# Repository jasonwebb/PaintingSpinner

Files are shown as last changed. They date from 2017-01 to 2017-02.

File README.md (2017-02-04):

# PaintingSpinner
Arduino-based hardware platform for interactively spinning a painting using a DC motor, infrared rangefinder and custom 3D printed components.

## Components

- Arduino Uno R3
- A [99:1, 300oz-in gearmotor](https://www.pololu.com/product/3207) driven by a [Cytron 10A DC Motor Driver Shield](http://www.robotshop.com/en/10a-dc-motor-driver-arduino-shield.html)
- Two 3W speakers driven by a [Cytron Easy MP3 Shield](http://www.robotshop.com/en/cytron-easy-mp3-shield.html)
- A [Sharp 2Y0A02 distance sensor](https://www.sparkfun.com/products/8958)
- Salvaged bicycle parts (chain, 26t and 14t gears)
- Various sizes of [scrap wood](https://github.com/jasonwebb/PaintingSpinner/blob/master/BOMs/Wood%20cutlist.csv)
- Various custom [3D printed parts](https://github.com/jasonwebb/PaintingSpinner/tree/master/CAD) designed in Fusion 360
- Various wood screws and angle brackets

## License
This work is licensed under a [Creative Commons Attribution-NonCommercial-ShareAlike 4.0 International License](http://creativecommons.org/licenses/by-nc-sa/4.0/).

Use this project to learn, tinker and share with friends. All commercial uses are forbidden without express written permission.



## Electronics architecture
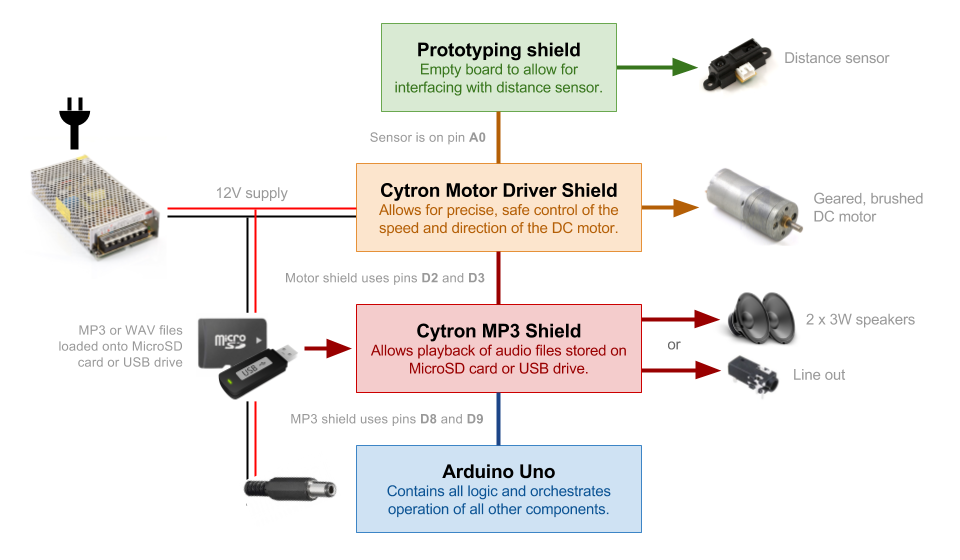
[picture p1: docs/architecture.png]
Architecture


## Mechanical assembly
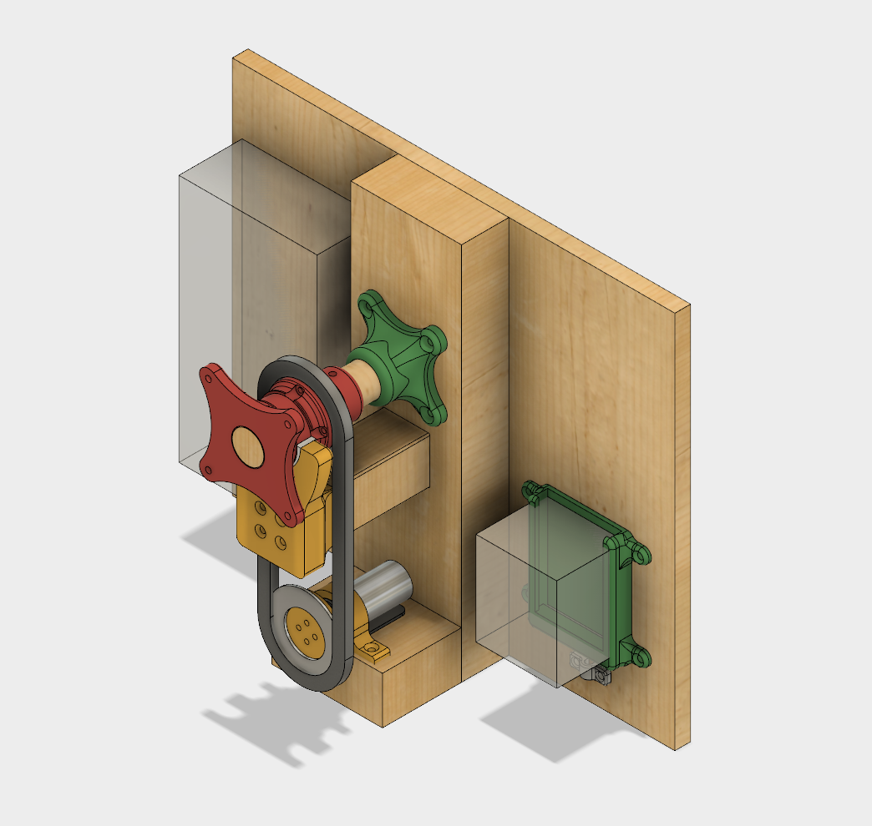
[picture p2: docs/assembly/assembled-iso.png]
Assembly


## Finished and installed
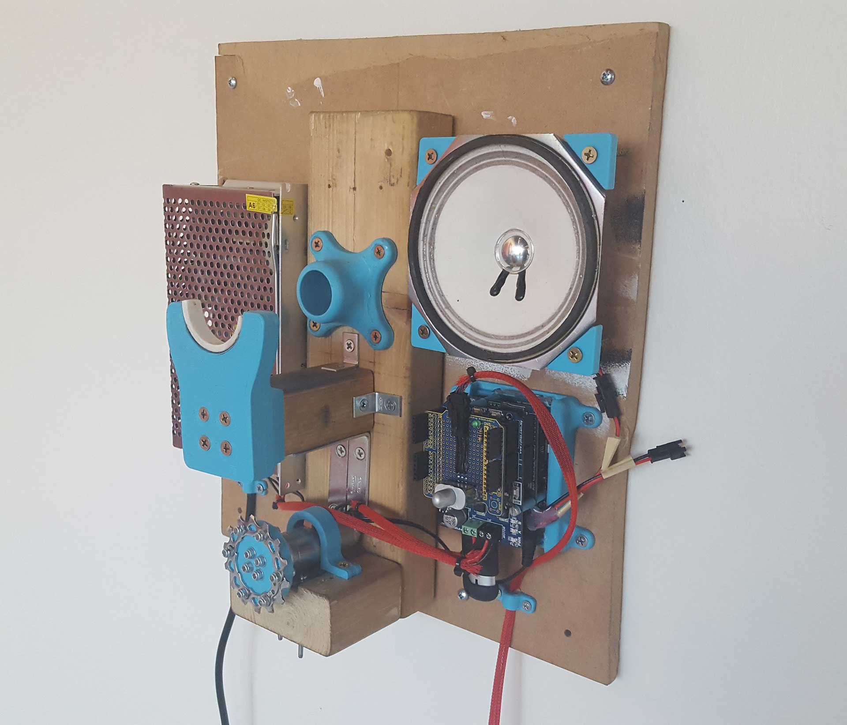
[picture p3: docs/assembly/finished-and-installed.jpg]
Finished and assembled


Nadia approaching

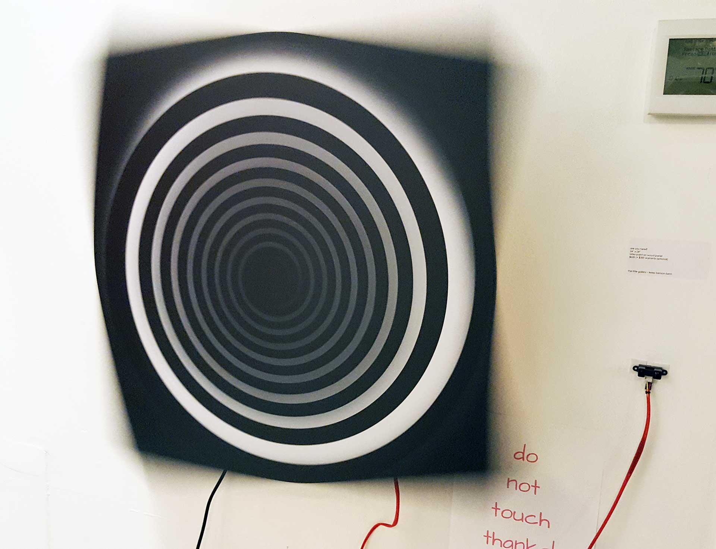
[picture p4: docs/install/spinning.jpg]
Spinning


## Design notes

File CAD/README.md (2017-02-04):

## Arduino stack standoffs
- Intended to guarantee uniform and reliable spacing between shields, reducing potential of shorts or disconnections due to tilting during use.
- Long standoffs (green) go between motor shield and audio shield.
- Short standoffs (yellow) go between audio shield and Arduino.
- Red washers go at very top of bolt.

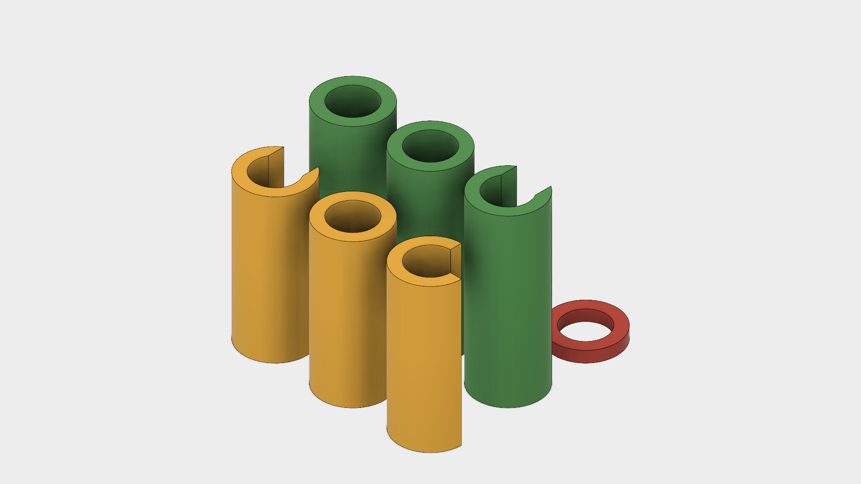
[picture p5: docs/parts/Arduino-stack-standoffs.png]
Arduino stack standoffs


## Axle support bracket
- Square cutout designed to loose friction fit with 2" square furring strip, which has nominal size of ~1.5".
- Circular cutout is made to fit half of a 1.5" diameter PVC tubing, cut to 1/2" in width. Use epoxy to join. This PVC inset will make direct contact with recessed ridge in "Compound pulley flange" allowing for smooth rotation and (hopefully) less friction.

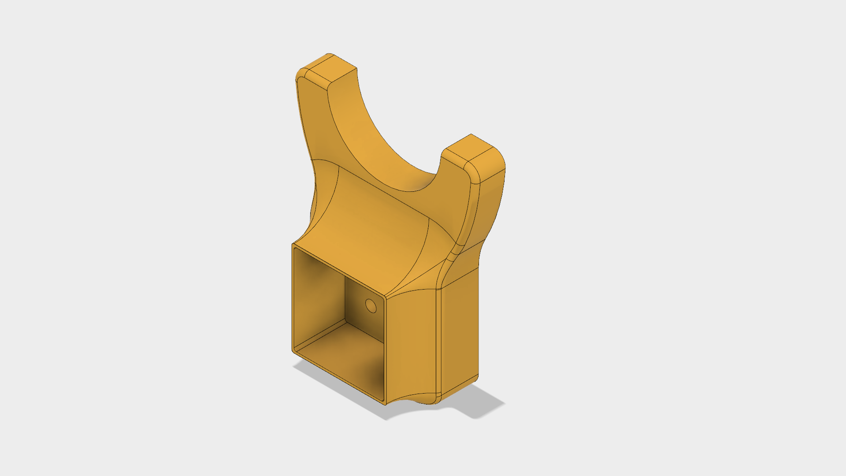
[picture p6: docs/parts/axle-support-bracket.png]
Axle support bracket


## Compound pulley flange
- One side (side with four arms) mounts to back of painting or piece to spin.
- Other side fits a 14t bicycle gear with particular hole pattern using M3 bolts.
   - Hole pattern is rotated to make it easier for a screwdriver to reach bolt heads for tightening / racheting.
- Includes a 1/2" wide recessed ridge meant to guide rotation of entire component along PVC inset on "Axle support bracket"
- A 1" wooden dowel goes through center hole, optionally fastened with small wood screw within recessed ridge. Make sure the head of the screw stays below diameter of this ridge to avoid interfering with rotation.

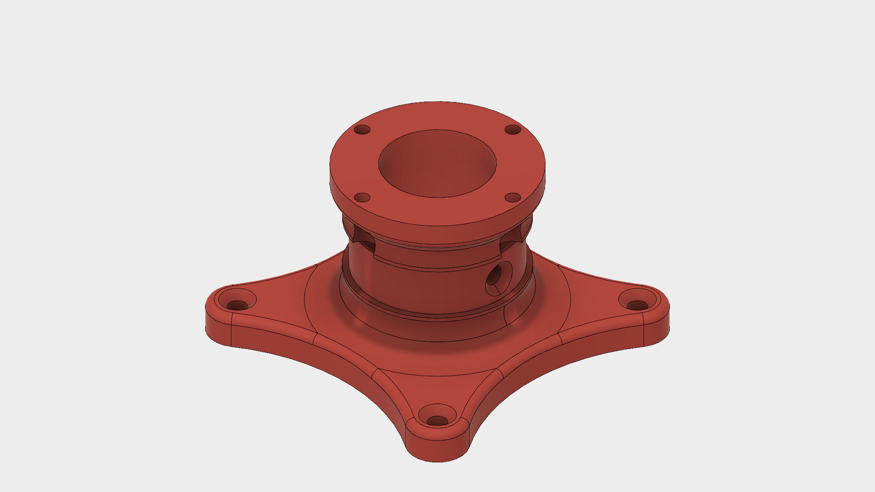
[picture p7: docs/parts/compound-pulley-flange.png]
Compound pulley flange


## Flange (right angle)
- Center hole has clearance fit allowance in order for 1" wood dowel to spin freely.
- Only meant to constrain wood dowel during rotation.

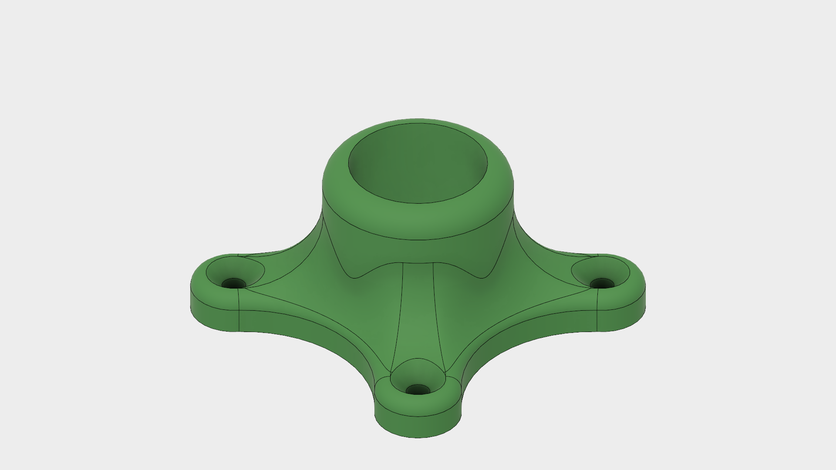
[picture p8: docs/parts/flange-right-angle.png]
Flange right angle


## Large pulley (26t) to Universal Mounting Hub adapter
- Allows for mounting of a 26t with a particular hole pattern to a Universal Mounting Hub from Pololu.
- Uses M4 bolts (with washers and lock nuts) to connect adapter to pulley.
- Uses M3 bolts (with lock nuts under adapter) to connect adapter to Universal Mounting Hub.

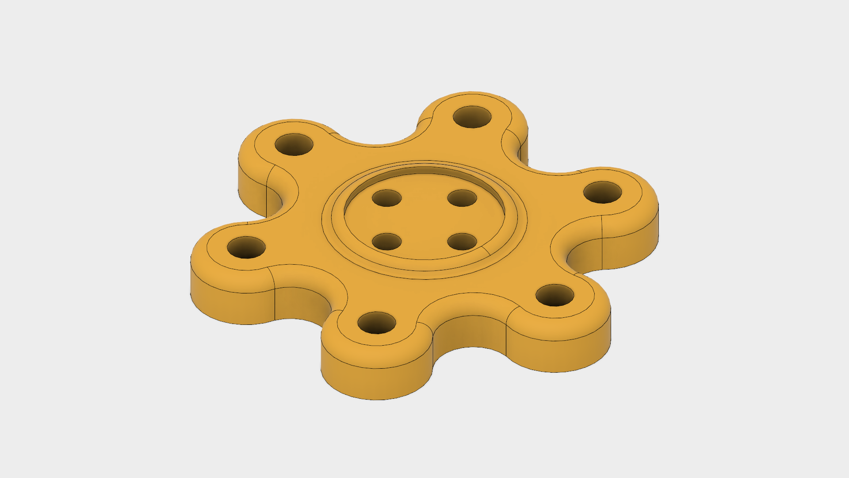
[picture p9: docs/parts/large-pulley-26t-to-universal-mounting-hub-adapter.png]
Large pulley (26t) to Universal Mounting Hub adapter


## Motor clamp
- Snuggly fits around gearmotor to help hold it in place. Use two wood screws to get desired level of tension.
- I recommend only using one directly over the gearbox, NOT the motor, to allow for better heat dissipation.

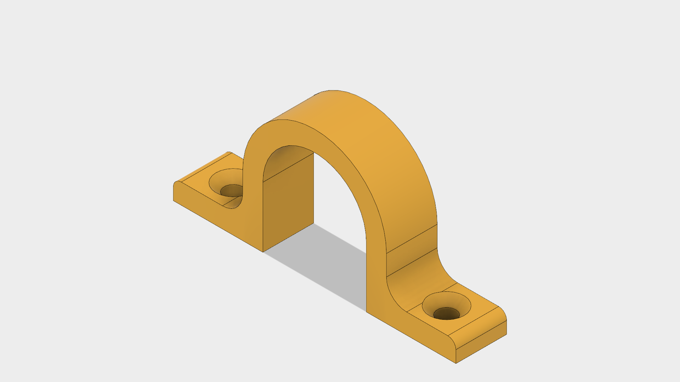
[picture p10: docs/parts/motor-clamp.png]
Motor clamp


## Small pulley (14t) flange
- Center hole fits 1" wood dowel.
- Meant to be bolted onto 14t bicycle gear with a particular hole pattern.
- Meant to accommodate M3 lock nuts with enough clearance to allow for a ratchet for easier tightening.

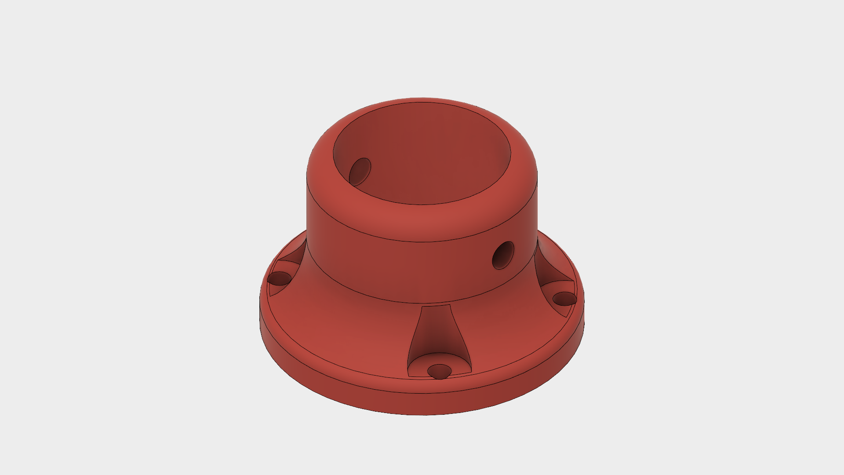
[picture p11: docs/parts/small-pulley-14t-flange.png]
Small pulley (14t) flange


## Small pulley (14t) to Universal Mounting Hub adapter
- Uses M3 bolts for all holes.
- Allows for use of drive pulley matching output pulley for better torque (at lower speed).

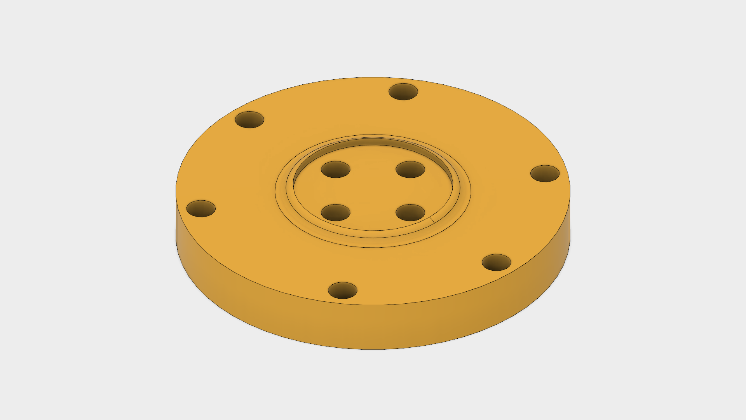
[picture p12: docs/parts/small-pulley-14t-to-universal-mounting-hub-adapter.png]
Small pulley (14t) to Universal Mounting Hub Adapter


## Speaker corner bracket
- Made to fit metal corner tabs for a particular speaker.

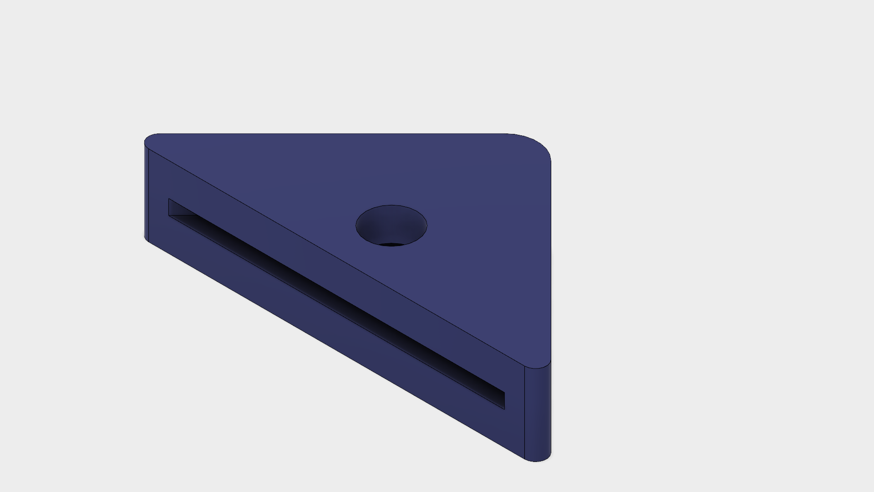
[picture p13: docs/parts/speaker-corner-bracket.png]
Speaker corner bracket


## Wire clamp
- Allows for strain relief for thicker wires, such as the AC power cord and sensor cable. Saves a trip to the hardware store at least.

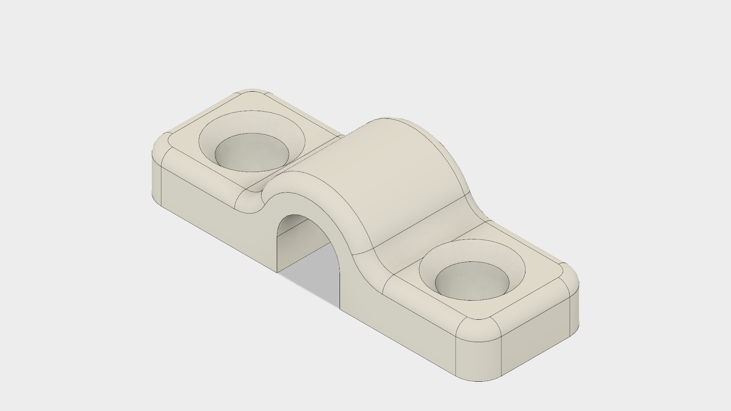
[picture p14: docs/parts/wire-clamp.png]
Wire clamp


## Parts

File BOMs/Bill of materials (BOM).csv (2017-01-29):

Part | Model name | Cost | Dealer | URL | Use
Motor | 99:1 Metal Gearmotor 25Dx54L mm HP 12V | $21.95 | Pololu | https://www.pololu.com/product/3207 | Uhm...it spins.
Mounting hub | Pololu Universal Aluminum Mounting Hub for 4mm Shaft, M3 Holes (2-Pack) | $6.95 | Pololu | https://www.pololu.com/product/1997 | Connecting motor shaft to painting
Motor mounting bracket | Pololu 25D mm Metal Gearmotor Bracket Pair | $7.45 | Pololu | https://www.pololu.com/product/2676 | Allows for easy, strong mounting of motor to box
Motor driver | 10A DC Motor Driver Arduino Shield | $15.75 | Robotshop | http://www.robotshop.com/en/10a-dc-motor-driver-arduino-shield.html | Allows Arduino to control the motor speed and direction
Arduino | Arduino Uno R3 (official) | $22.39 | Robotshop | http://www.robotshop.com/en/arduino-uno-r3-usb-microcontroller.html | Contains all logic and coordinates all other components
MP3 shield | Cytron Easy MP3 Shield | $17.06 | Robotshop | http://www.robotshop.com/en/cytron-easy-mp3-shield.html | Allows Arduino to play and control audio - can play through 3 small speakers or audio cable
SD card or USB drive | {On hand?} |  |  |  | Stores MP3 files for playback
Speakers | {Need two 3W speakers - on hand?}
Power supply | LEDMO 12V @ 20A power supply | $17.99 | Amazon | https://smile.amazon.com/LEDMO-Switching-Converter-Adapter-Transformer/dp/B01E6S0JS4 | Supplies power to everything
Prototyping shield | ProtoShield Short Prototyping Board for Arduino | $2.25 | Robotshop | http://www.robotshop.com/en/protoshield-short-prototyping-board-arduino.html | Allows for freeform interfacing with sensor(s)
Distance sensor | Sharp GP2Y0A02YK0F | $14.95 | Sparkfun | https://www.sparkfun.com/products/8958 | Sensing the viewer for interactivity
 | Total | $126.74

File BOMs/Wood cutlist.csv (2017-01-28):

Name | Material | Dimension(s) - inch | Dimension(s) - mm
Axle | 1" wood dowel | 5 in
Axle support | 2" square furring strip | 3.89 in | 98.806mm
Motor support | 2x4" stud | 2.5 in
Mounting spine | 2x4" stud | 12 in
Mounting plate | Plywood - 0.5" or more | At least 14x12"

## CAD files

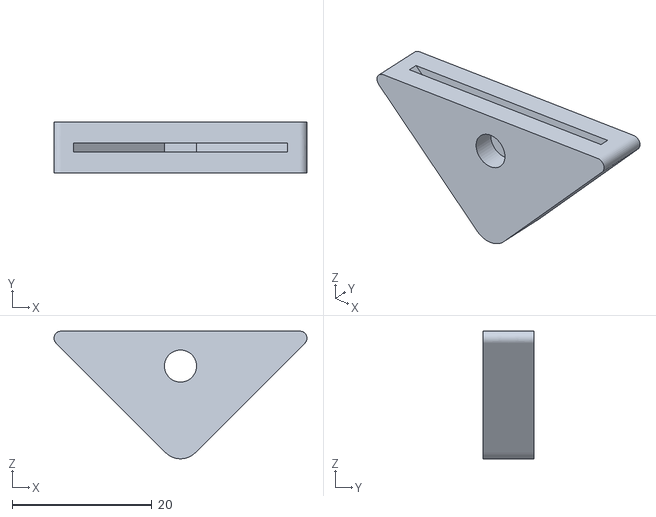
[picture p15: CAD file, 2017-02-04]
CAD/speaker-corner-bracket.stl
36.3 x 7.35 x 18.3

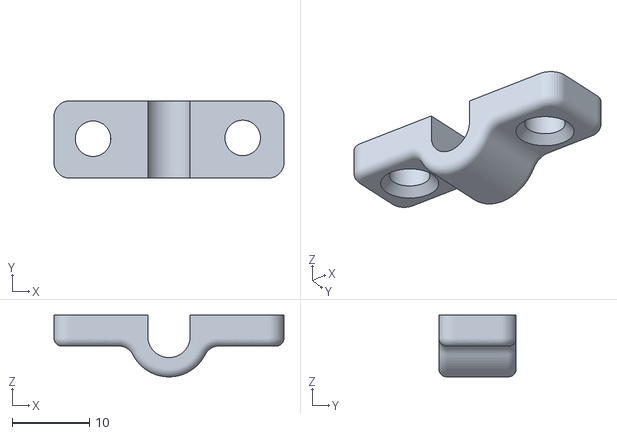
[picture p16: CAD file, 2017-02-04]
CAD/wire-clamp.stl
29.8 x 10.0 x 7.99

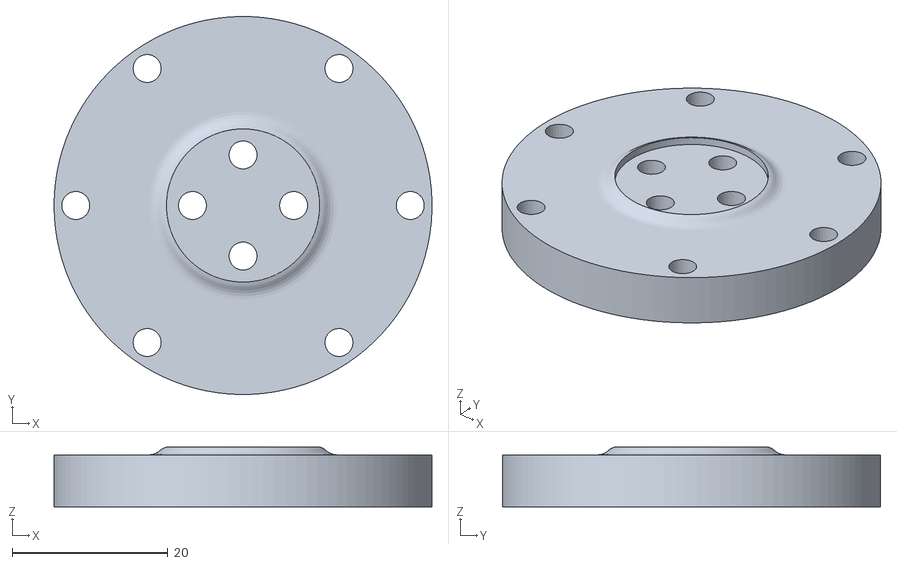
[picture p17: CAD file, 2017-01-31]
CAD/small-pulley-(14t)-to-universal-mounting-hub-adapter.stl
48.6 x 48.6 x 7.70

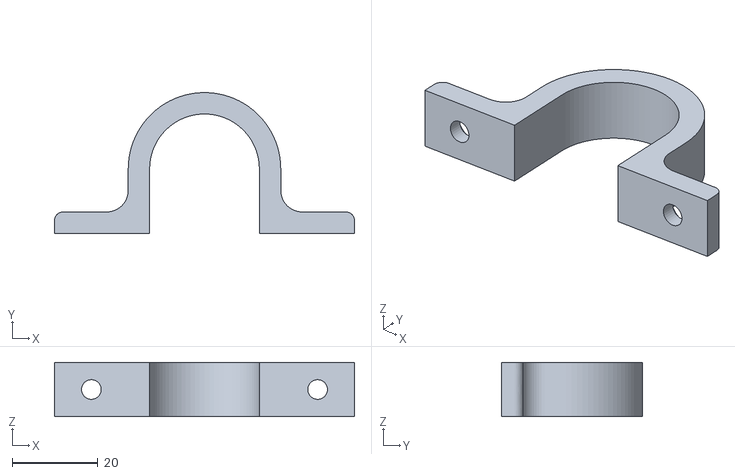
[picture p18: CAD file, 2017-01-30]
CAD/motor-clamp.stl
70.0 x 32.8 x 12.6

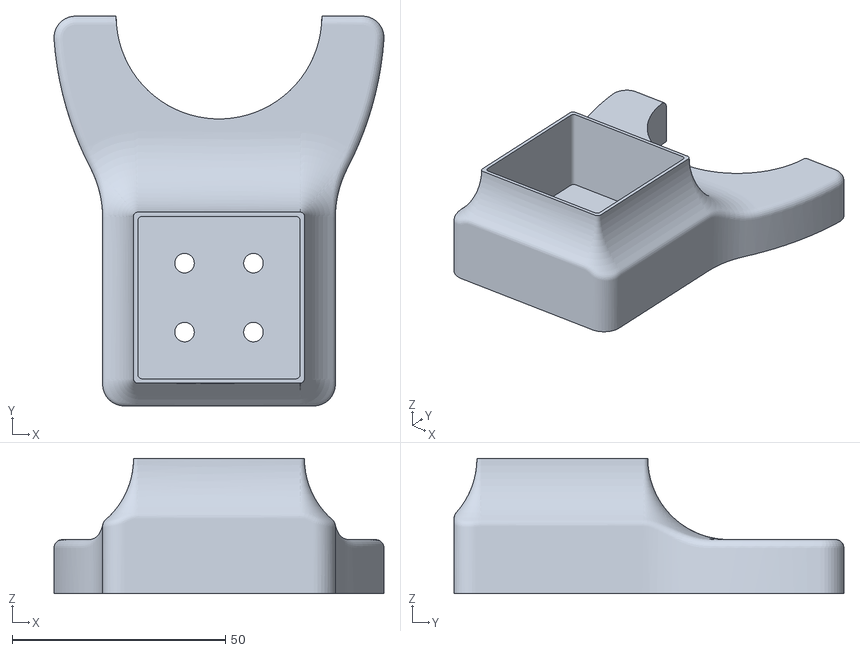
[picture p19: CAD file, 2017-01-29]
CAD/axle-support-bracket.stl
77.4 x 91.5 x 31.8

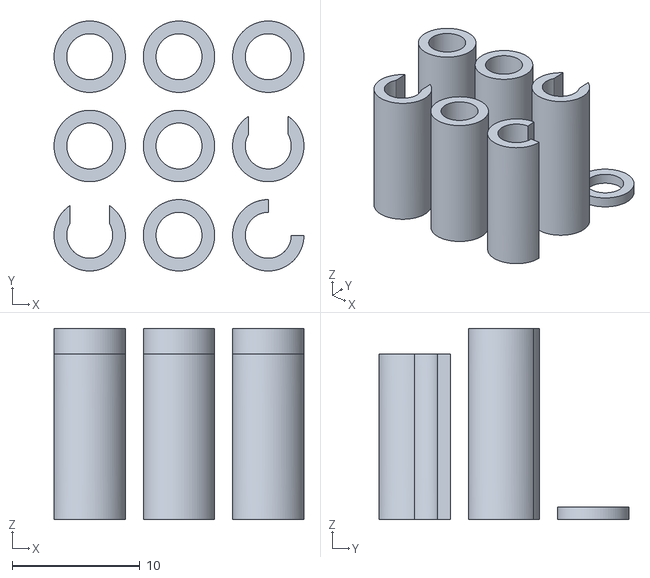
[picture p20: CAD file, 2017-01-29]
CAD/Arduino-stack-standoffs.stl
19.6 x 19.6 x 15.0

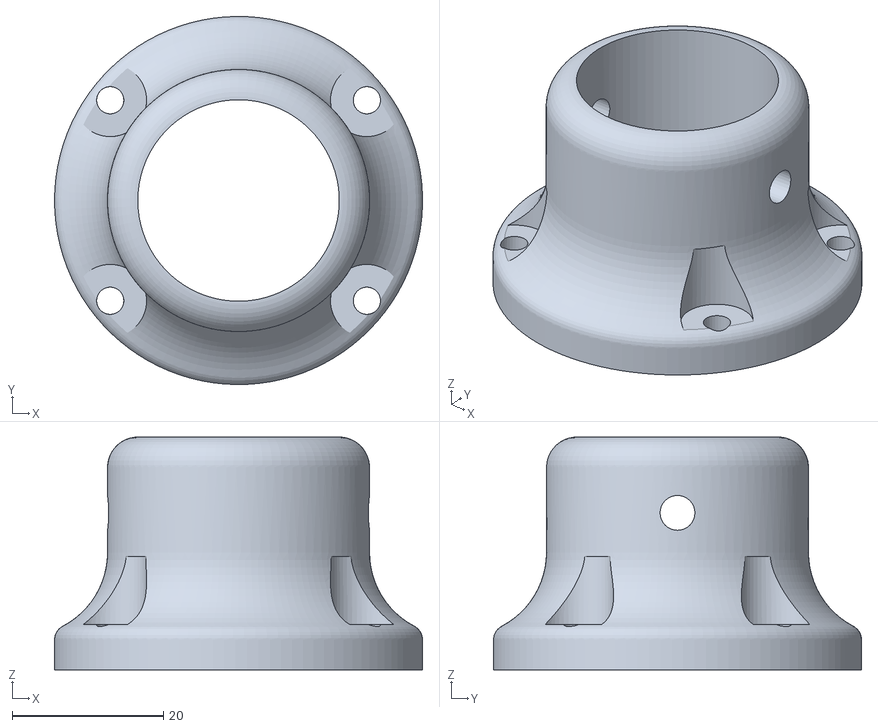
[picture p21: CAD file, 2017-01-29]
CAD/small-pulley-(14t)-flange.stl
48.6 x 48.6 x 30.8

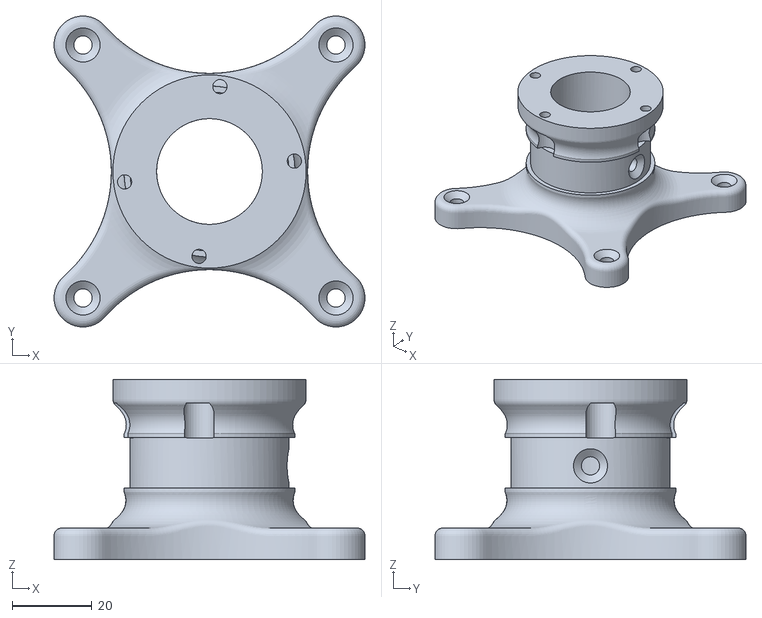
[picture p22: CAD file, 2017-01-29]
CAD/compound-pulley-flange.stl
78.2 x 78.2 x 45.4

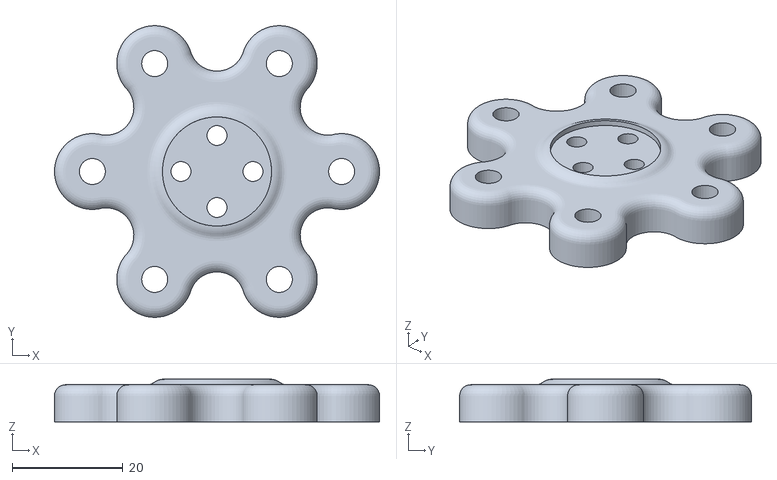
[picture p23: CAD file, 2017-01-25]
CAD/large-pulley-(26t)-to-universal-mounting-hub-adapter.stl
58.7 x 52.7 x 7.70

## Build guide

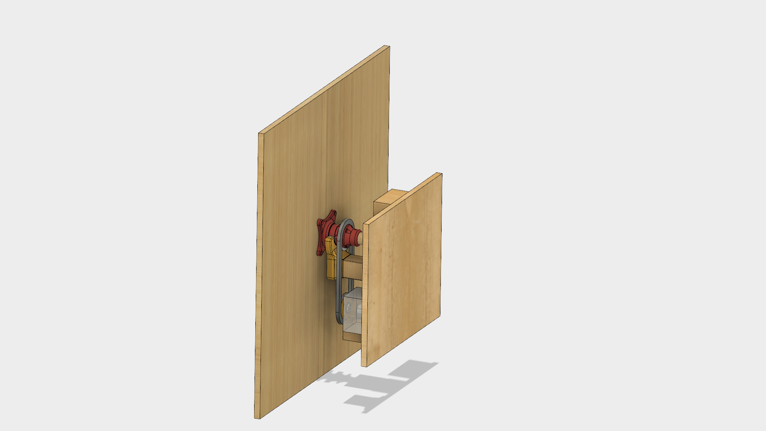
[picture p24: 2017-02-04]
docs/assembly/assembled-with-painting.png

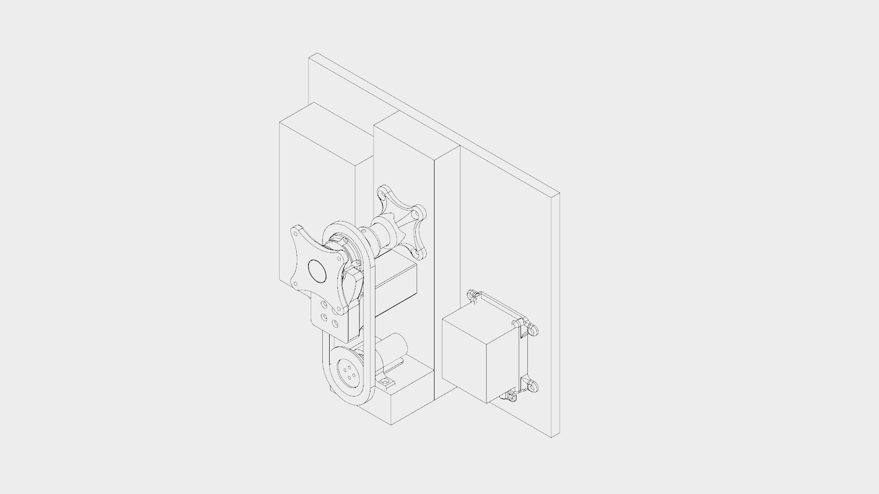
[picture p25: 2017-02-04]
docs/assembly/assembled-iso-wireframe.png

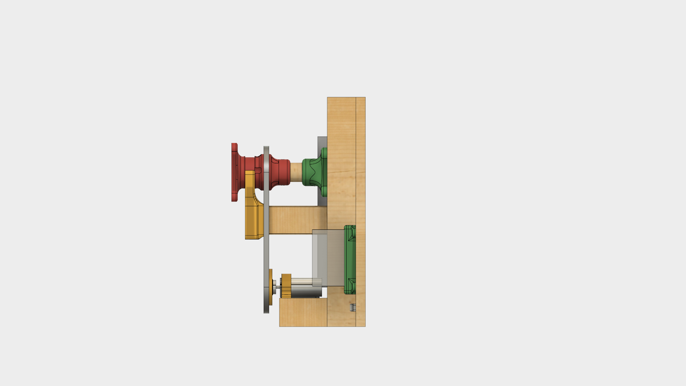
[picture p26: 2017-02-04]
docs/assembly/assembled-side.png

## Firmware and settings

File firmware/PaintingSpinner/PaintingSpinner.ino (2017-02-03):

/***************************************************************
 * PaintingSpinner
 * Built by Jason Webb for artist Nadia Shinkunas
 * 
 * Github repo: https://github.com/jasonwebb/PaintingSpinner
 * Author website: http://jason-webb.info
 ***************************************************************/

#include <CytronEZMP3.h>

/*******************************
* Motor parameters
********************************/
const byte CW = HIGH;
const byte CCW = LOW;

byte motorDirection = CCW;

byte motorPwmPin = 3;
byte motorDirPin = 2;

int motorCurrentSpeed = 0;
int motorTargetSpeed = 0;
int motorMinSpeed = 75;
int motorMaxSpeed = 255;
int motorAcceleration = 1;

boolean motorEnabled = true;

long motorUpdateInterval = 175;  // (in ms) faster updates mean faster acceleration, so keep them slow 
                                // (high values) to prevent too much torque on motor gears.

unsigned long motorRandomUpdateLower = 20 * 1000,
              motorRandomUpdateUpper = 50 * 1000;
unsigned long motorRandomUpdateInterval = 0;

unsigned long motorLastUpdate = 0;
unsigned long motorLastRandomUpdate = 0;


/*******************************
* Audio shield parameters
********************************/
CytronEZMP3 audio;

byte audioRxPin = 8;
byte audioTxPin = 9;

byte audioTrackNumber = 1;
byte audioTracksTotal;

byte audioVolume = 30;
byte audioMinVolume = 10;
byte audioMaxVolume = 30; // seems to be a hard limit either of the library, chip or physics

boolean audioEnabled = false;

int audioUpdateInterval = 1000; // Cytron MP3 library/chip is slow and prone to crashing, so keep updates low

unsigned int audioRandomUpdateLower = 10 * 1000,
             audioRandomUpdateUpper = 30 * 1000;
unsigned int audioRandomUpdateInterval = 0;

unsigned int audioLastUpdate = 0;
unsigned int audioLastRandomUpdate = 0;


/*******************************
* Distance sensor parameters
********************************/
byte sensorPin = A0;
byte sensorEnableSwitchPin = A1;
byte sensorEnabledLEDPin = A3;

// Rolling average variables
const int sensorNumSamples = 50;
int sensorSamples[sensorNumSamples];
int sensorSampleIndex = 0;
int sensorTotal = 0;
int sensorAverage = 0;

boolean sensorEnabled, sensorEnabledNextState;

unsigned long sensorUpdateInterval = 10;
unsigned long sensorLastUpdate = 0;

int sensorLowestValue = 50;   // represents furthest distance from sensor
int sensorHighestValue = 516; // represents closest distance to sensor

int sensorMinimumThreshold = 50;  // filter out sensor noise to allow motor to completely stop when people leave


/**************************************
* General state flags and variables
***************************************/
boolean DEBUG = true;
unsigned long currentTime = 0;


void setup() {
  // Initialize debug mode ----------------------------------------
  if (DEBUG) {
    Serial.begin(9600);
    while(!Serial);
  }

  // Randomize random seed ----------------------------------------
  randomSeed(analogRead(A5));

  // Initialize motor driver shield -------------------------------
  pinMode(motorPwmPin, OUTPUT);
  pinMode(motorDirPin, OUTPUT);

  analogWrite(motorPwmPin, motorCurrentSpeed);  // Should be 0
  digitalWrite(motorDirPin, motorDirection);

  if(DEBUG)
    Serial.println("Motor ready");


  // Initialize audio shield --------------------------------------
  if (!audio.begin(audioRxPin, audioTxPin)) {
    if (DEBUG)
      Serial.println("Failed to initialize audio shield");

    while (1);
  }
  
  audio.setVolume(audioVolume);

  audioTracksTotal = audio.getTotalFiles();

  if(DEBUG)
    Serial.println("Audio shield ready");
      

  // Initialize sensor --------------------------------------------
  pinMode(sensorPin, INPUT);
  pinMode(sensorEnableSwitchPin, INPUT);
  pinMode(sensorEnabledLEDPin, OUTPUT);

  // Activate internal pull-up for enable switch
  digitalWrite(sensorEnableSwitchPin, HIGH);

  // Set up initial enable state
  sensorEnabled = digitalRead(sensorEnableSwitchPin);
  digitalWrite(sensorEnabledLEDPin, sensorEnabled);

  // Get initial switch state
  updateSensorEnabledSwitch();

  // Initialize sample buffer to empty values
  for(int i = 0; i < sensorNumSamples; i++)
    sensorSamples[i] = 0;

  if(DEBUG) {
    Serial.println("Distance sensor ready");

    switch(sensorEnabled) {
      case HIGH:
        Serial.println("Distance sensing is enabled - motor speed now mapped to distance");
        break;
      case LOW:
        Serial.println("Distance sensing is disabled - motor speed now randomized at random intervals");
        break;
    }
  }
}

void loop() {
  currentTime = millis();

  // Check for and process new sensor data for use in upcoming logic
  // - Takes readings from the distance sensor (if enabled)
  // - Checks the sensor enable switch for changes
  updateSensor();

  // Update motor speed to chase a target speed
  // - If sensor is enabled, target speed will follow distance sensor
  // - If sensor is NOT enabled, target speed will be randomized at random intervals
  updateMotor();

  // Update audio
  // - If sensor is enabled, trigger samples continuously and map sensor average to volume
  // - If sensor is NOT enabled, trigger samples at random volumes at random intervals
  updateAudio();

}

/******************************************************************************
* Update sensor data buffer and calculated values
*   - Takes readings from the distance sensor (if enabled)  
*   - Checks the distance sensor enable switch for changes
******************************************************************************/
void updateSensor() {
  if(currentTime - sensorLastUpdate >= sensorUpdateInterval) {
    // Check and update enable switch
    updateSensorEnabledSwitch();
    
    // Update rolling average of samples ---------------------------    
    // Pop latest sample from total
    sensorTotal -= sensorSamples[sensorSampleIndex];
  
    // Get new sample from the sensor and store it in buffer
    sensorSamples[sensorSampleIndex] = analogRead(sensorPin);
  
    // Push latest sample to total
    sensorTotal += sensorSamples[sensorSampleIndex];
  
    // Advance or roll over buffer index
    if(sensorSampleIndex < sensorNumSamples - 1)
      sensorSampleIndex++;
    else
      sensorSampleIndex = 0;
  
    // Calculate new average
    sensorAverage = sensorTotal / sensorNumSamples;

    sensorLastUpdate = millis();
  }
}

/******************************************************************************
* Check for and process any changes to the "enable" switch
*   - If a change is detected, some prep work needs to happen
******************************************************************************/
void updateSensorEnabledSwitch() {
  // Check enable switch pin
  sensorEnabledNextState = digitalRead(sensorEnableSwitchPin);

  if(sensorEnabledNextState != sensorEnabled) {
    switch(sensorEnabledNextState) {
      case HIGH:
        digitalWrite(sensorEnabledLEDPin, HIGH);
        motorRandomUpdateInterval = (int)random(motorRandomUpdateLower, motorRandomUpdateUpper);

        if(DEBUG)
          Serial.println("Turning on distance sensing");

        break;
        
      case LOW:
        digitalWrite(sensorEnabledLEDPin, LOW);

        if(DEBUG)
          Serial.println("Turning off distance sensing");

        break;
    }
    
    sensorEnabled = sensorEnabledNextState;
  }
}

/*******************************************************************************************
* Update motor target speed and current speed
*   - If sensor is enabled, target speed will follow distance sensor
*   - If sensor is NOT enabled, target speed will be randomized at random intervals
*   - It is very important to keep accelerations low to prevent too much torque on motor
********************************************************************************************/
void updateMotor() {
  if(currentTime - motorLastUpdate >= motorUpdateInterval && motorEnabled) {
    // If sensor is enabled, map live sensor data to target motor speed
    if(sensorEnabled) {      
      if(sensorAverage > sensorMinimumThreshold)
        motorTargetSpeed = constrain(map(sensorAverage, sensorLowestValue, sensorHighestValue, motorMinSpeed, motorMaxSpeed), motorMinSpeed, motorMaxSpeed);
      else
        motorTargetSpeed = 0;

    // If sensor is NOT enabled, generate new random target speeds at random intervals
    } else {
      // Choose random target speed and new random update interval
      if(currentTime - motorLastRandomUpdate >= motorRandomUpdateInterval) {
        motorTargetSpeed = (int)random(motorMinSpeed, motorMaxSpeed);
        motorRandomUpdateInterval = random(motorRandomUpdateLower, motorRandomUpdateUpper);

        if(DEBUG) {
          Serial.print("New target speed - ");
          Serial.print(map(motorTargetSpeed, 0, motorMaxSpeed, 0, 100));
          Serial.println("%");
        }

        motorLastRandomUpdate = millis();
      }
    }

    // Adjust current speed to "chase" target speed, within bounds
    if( (motorCurrentSpeed < motorTargetSpeed) && (motorCurrentSpeed < motorMaxSpeed) )
        motorCurrentSpeed += motorAcceleration;
    else if( (motorCurrentSpeed > motorTargetSpeed) && (motorCurrentSpeed > 0) )
        motorCurrentSpeed -= motorAcceleration;
  
    // Push motor speed to motor shield
    analogWrite(motorPwmPin, motorCurrentSpeed);

    motorLastUpdate = millis();
  }
}

/*****************************************************************
 * Update audio
******************************************************************/
void updateAudio() {
  if(currentTime - audioLastUpdate >= audioUpdateInterval && audioEnabled) {
      if(1) {
//    if(!audio.isPlaying()) {
      // If sensor is enabled, map distance to volume
      if(sensorEnabled) {
        audioVolume = (int)constrain(map(sensorAverage, sensorLowestValue, sensorHighestValue, audioMinVolume, audioMaxVolume), audioMinVolume, audioMaxVolume);

        audioTrackNumber = (int)random(1,audioTracksTotal);
        audio.setVolume(audioVolume);
        audio.playTrack(audioTrackNumber);

        if(DEBUG)
          Serial.println("Triggering audio file");
        
      // If sensor is NOT enabled, just use max volume
      } else {
        if(currentTime - audioLastRandomUpdate >= audioRandomUpdateInterval) {
          audioVolume = audioMaxVolume;

          audioTrackNumber = (int)random(1,audioTracksTotal);
          audio.setVolume(audioVolume);
          delay(100);
          audio.playTrack(audioTrackNumber);
          delay(100);

          if(DEBUG) {
            Serial.print("Triggering audio file - ");
            Serial.println(audioTrackNumber);
          }

          audioRandomUpdateInterval = (int)random(audioRandomUpdateLower, audioRandomUpdateUpper);
          audioLastRandomUpdate = millis();
        }
      }

      audioLastUpdate = millis();
    }
  }
}

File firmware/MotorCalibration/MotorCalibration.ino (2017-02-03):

/***************************************************************
 * PaintingSpinner - motor calibration
 * Built by Jason Webb for artist Nadia Shinkunas
 * 
 * DESCRIPTION:
 * Revs up and down motor speed to (1) verify operation and
 * (2) allow for quick tuning of program variables.
 * 
 * Github repo: https://github.com/jasonwebb/PaintingSpinner
 * Author website: http://jason-webb.info
 ***************************************************************/

/*******************************
* Motor parameters
********************************/
const boolean CW = LOW;
const boolean CCW = HIGH;

boolean motorDirection = CW;

byte motorPwmPin = 3;
byte motorDirPin = 2;

int motorSpeed = 0;
int motorMaxSpeed = 255;
int motorAcceleration = 1;

const boolean UP = 0;
const boolean DOWN = 1;

boolean rampDirection = UP;

int motorUpdateInterval = 50;  // in milliseconds
unsigned int motorLastUpdate = 0;

/**************************************
* General state flags and variables
***************************************/
boolean DEBUG = true;
unsigned int currentTime = 0;

void setup() {
  // Initialize debug mode ---------------------------------------
  if (DEBUG) {
    Serial.begin(9600);
    while(!Serial);
  }

  // Initialize motor driver shield -------------------------------
  pinMode(motorPwmPin, OUTPUT);
  pinMode(motorDirPin, OUTPUT);

  analogWrite(motorPwmPin, motorSpeed);
  digitalWrite(motorDirPin, motorDirection);

  if(DEBUG)
    Serial.print("Ramping up (CW) ... ");
}

void loop() {
  currentTime = millis();

  // Update motor speed and direction  ----------------------------------------------------
  if(millis() > motorLastUpdate + motorUpdateInterval) {
    switch(rampDirection) {
      // Ramp up in current direction, then flip to ramp down mode
      case UP:
        if(motorSpeed < motorMaxSpeed) {
          motorSpeed += motorAcceleration;
        } else {
          rampDirection = DOWN;
  
          if(DEBUG) {
            Serial.println("done");
      
            if(motorDirection == CW)
              Serial.print("Ramping down (CW) ... ");
            else
              Serial.print("Ramping down (CCW) ... ");
          }
        }
  
        break;
  
      // Ramp down in current direction, then flip to ramp up mode and flip direction
      case DOWN:
        if(motorSpeed > 0) {
          motorSpeed -= motorAcceleration;
        } else {
          rampDirection = UP;
  
          if(DEBUG)
            Serial.println("done");          
  
          if(motorDirection == CW) {
            motorDirection = CCW;
  
            if(DEBUG)
              Serial.print("Ramping up (CCW) ... ");
          } else {
            motorDirection = CW;
  
            if(DEBUG)
              Serial.print("Ramping up (CW) ... ");
          }
        }
  
        break;
    }

    motorLastUpdate = millis();
  }

  // Push most recent direction and speed to shield
  digitalWrite(motorDirPin, motorDirection);
  analogWrite(motorPwmPin, motorSpeed);
}

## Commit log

2017-01-20 Initial commit - firmware, BOM, datasheets
    [Bill of materials (BOM).csv]
2017-01-24 Added distance sensor datasheet
2017-01-25 Added prototype CAD files
    [compound-pulley-flange.stl, pulley-(26t)-to-universal-mounting-hub-adapter.stl]
2017-01-25 Updated pulley adapter model, added motor test Arduino sketch
    [pulley-(26t)-to-universal-mounting-hub-adapter.stl]
2017-01-26 Updated motor calibration sketch
2017-01-26 Added sensor calibration sketch
2017-01-27 Updated sensor calibration sketch
2017-01-28 Added wood cutlist
    [Wood cutlist.csv]
2017-01-28 Updated BOM
    [Bill of materials (BOM).csv, Wood cutlist.csv]
2017-01-29 Updated + added CAD files
    [compound-pulley-flange.stl, large-pulley-(26t)-to-universal-mounting-hub-adapter.stl, pulley-(26t)-to-universal-mounting-hub-adapter.stl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]
2017-01-29 Added Arduino stack standoffs CAD file
    [Arduino-stack-standoffs.stl]
2017-01-29 Added assembly images, updated BOM and README
    [Bill of materials (BOM).csv]
2017-01-29 Added renders for all CAD files, updated main README
    [axle-support-bracket.stl]
2017-01-29 Updated CAD README
2017-01-30 Added motor clamp CAD file, updated CAD README
    [motor-clamp.stl]
2017-01-31 Added Arduino sketch to test audio system
2017-01-31 Added alternative 14t drive gear adapter
    [small-pulley-(14t)-to-universal-mounting-hub-adapter.stl]
2017-01-31 Updated sensor and motor calibration sketches
2017-02-02 Updated primary firmware Arduino
2017-02-04 Added CAD files for wire clamp and speaker corner bracket
    [speaker-corner-bracket.stl, wire-clamp.stl]
2017-02-04 Updated assembly images and main README
